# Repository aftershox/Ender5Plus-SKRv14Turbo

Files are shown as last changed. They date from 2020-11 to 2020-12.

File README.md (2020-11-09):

# Ender5Plus-SKRv14Turbo
All things related to my Ender 5 Plus

# 16th October 2020 - _Printer arrives_

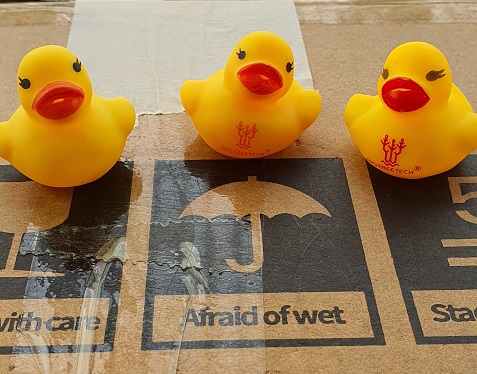
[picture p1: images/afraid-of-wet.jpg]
Image of ducks


**Stock Machine**
BUILT and TESTED - running 1.70.2 firmware from factory.  
- _**BUG found**_ - Auto Home puts NOZZLE and not BL Touch Probe pin at centre of bed.

---

Communicating with the Mainboard
- To connect to the mainboard from PC to USB - have to install FTDI drivers - https://support.th3dstudio.com/hc/en-us/articles/360043291472-Creality-Printer-Drivers-FT232R-Chip-Most-Models
- - Used the FTDI F232R Windows Drivers to create COM port for accessing the Creality Mainboard 
- Use Pronterface to capture existing setup

Firmware for Stock Creality board
- Firmware upgraded to Kersey Fabs Ender-(5PlusBLTouch_0904_V1.71.0 KF.hex) - to fix the BL Touch probe offset (Probe now in centre of bed)
> Watch the video and check Video Description for download links - https://youtu.be/9pDoxf13_wg

- Once Firmware is upgraded - the menus revert back to Chinese Language, so use the control panel / touch screen to set back to English Language. 

# 25th October 2020 - Next job is to install SKR Turbo v.1.4 with 5 x TMC2209s and Z-Steppers auto-align G34 and the BTT TFT 3.5"

1) Set jumpers on SKR v.1.4 Turbo - as per the BTT Guide for TMC 2209 Drivers in UART mode
- - Remove 3 x jumpers from each stepper installation location - leaving just one

2) If NOT using Stallguard / Sensorless Homing - you'll need to CUT the Diag pins on EACH Driver that uses a Physical Limit Switch
- X-UART (Cut Pin / Uses Physical Switch for X Endstop)
- Y-UART (Cut Pin / Uses Physical Switch for Y Endstop)
- Z-UART (CUT PIN / Uses BL Touch Probe as Z- MIN Endstop)
- E0-UART (Cut Pin / Uses Filament Runout Sensor [Physical Switch] with Extruder)
- E1-UART (used for SECOND Z Stepper Motor) - CUT PIN - as BL Touch Probe uses Z- MIN for Z Endstop

- If using 5 x TMC 2209 - i.e. to setup Z2 for using G34 - Z Steppers Auto-Alignment
- - Install TMC 2209 #5 into the E1-UART (Z2) socket
- - E1-UART [Used for Z2-UART) (DO NOT CUT PIN / Uses BL Touch Probe as Endstop)

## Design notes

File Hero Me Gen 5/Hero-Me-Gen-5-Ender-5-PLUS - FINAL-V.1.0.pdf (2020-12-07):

## Installing the HMG5 / Hero Me Gen 5 on the Ender 5 PLUS (Hotend in original build OEM format) 3dpmarkr / aftershox (Github)

This is my guide to installing the Hero Me Gen 5 onto a Creality Ender 5 PLUS – that has not been modified. e.g. Original Hot End housing and fans, as shipped (with no frame modifications). It uses the most compact parts for the smallest footprint, and DUAL 4020 Radial Blowers for maximum CFM / reduced noise overhead as the dual fans can be run as low as 50% without compromising air flow.

TOTAL 3D PRINTED PARTS 7 + 1 OPTIONAL.

GANTRY PARTS
Ender_OEM-MS_Gantry_Adapter_4A

BASE
Hero_Me_Gen5_Base_1

DUCTS
4020_Left_Fan_Mount_Spacer 4020_Lightweight_Duct_Standard_Left

4020_Lightweight_Duct_Standard_Right

ABL – BL TOUCH v.3.1.
BLTouch_Wing_Compact
with the BLTouch_Slider_Compact
X -38, Y+6

OEM 4010 AXIAL FAN COVER (OPTIONAL)
HMG5_Turbine_Fan_Guard

NOTE : The following parts have been chosen to take up the MINIMUM AMOUNT of space. Some of the HMG5 DUCT options protrude too far forward, so with an Ender 5 PLUS – these are the most COMPACT parts. IF you have moved your front TOP extrusion down (for Nozzle visibility) then you may be able to use a different DUCT. If, however, your printer is in the original OEM frame format – then please use the parts list (shown above) to prevent your Hotend crashing into the frame etc.

HMG5 Installation Guide Version 1.0– Written by 3dmarkr / aftershox – 7th December 2020 Page 1 of 28

B.O.M - FANS
2 | x | 4020 Radial Blower – 24V – Dual Ball Bearing type

B.O.M. - Electronics / Connectors / Wire etc.
1 | x | T shape QUICK-Splice Connector.
1 | x | 100mm length Silcone Wire (YELLOW)
- 24 AWG Electrical Wire Kit,0.20mm² Flexible Silicone Wire - rated 300V Hookup
| | Wire High Temperature Resistance
1 | x | 100mm length Silicone Wire (BLUE)
- 24 AWG Electrical Wire Kit,0.20mm² Flexible Silicone Wire - rated 300V Hookup
| | Wire High Temperature Resistance
2 | x | JST.SM 2.54 connectors (2 pin) MALE / FEMALE
1 | x | Tube of Superglue (for securing your nuts!)
2 | x | Small 10mm lengths of heat shrink tubing YELLOW (OPTIONAL)

B.O.M - Screws, bolts & fixings

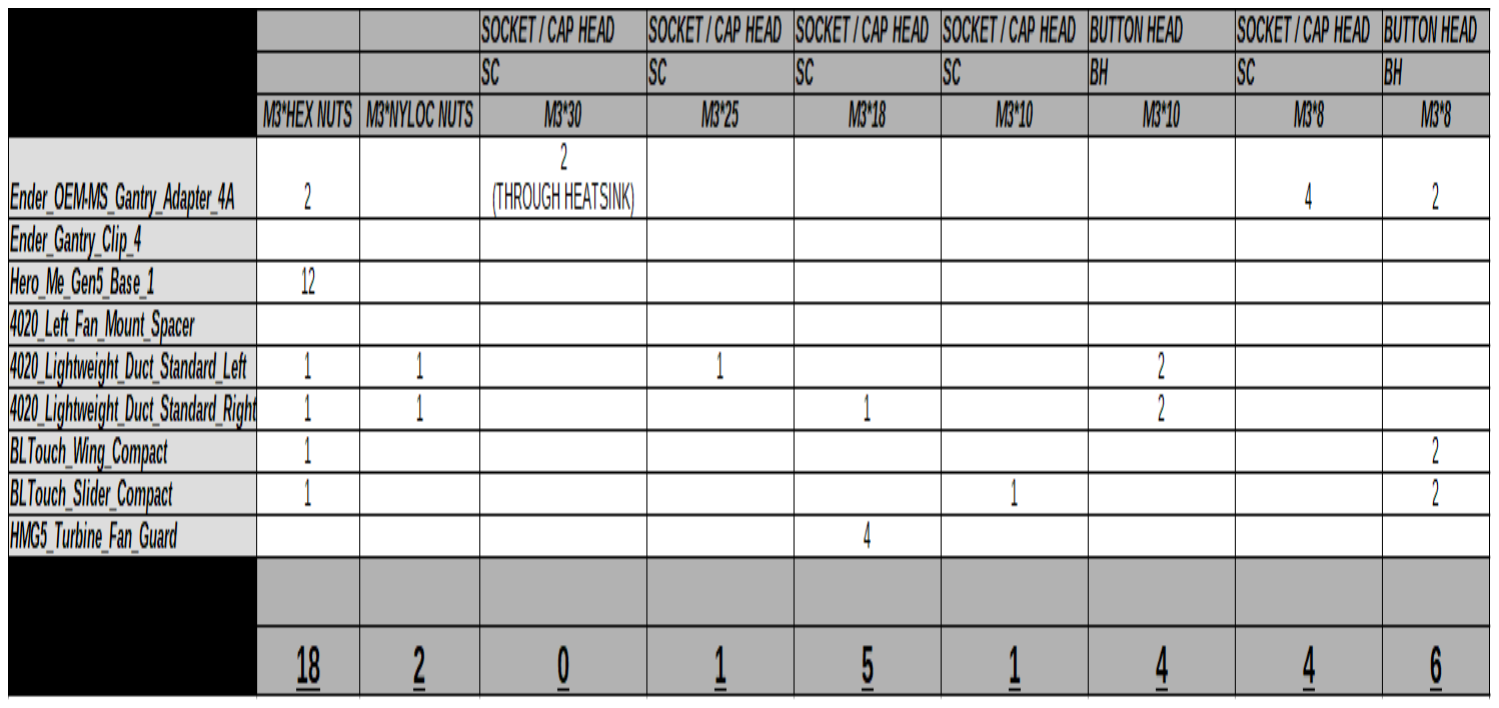
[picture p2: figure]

HMG5 Installation Guide Version 1.0– Written by 3dmarkr / aftershox – 7th December 2020 Page 2 of 28

TOOLS / SUNDRIES

IWISS SN-01BM Ratchet Wire Cable Crimping Pliers Tool 0.08-0.5mm² or SIMILAR Wire Cutters
Hex Keys / Hex Drivers (supplied with printer)
Spanners (in particular, the Nozzle spanner)
3mm drill bit / Cable Ties

### Installation – Notes

Wiring – Preparation

To upgrade from a single 4010 Radial Fan Blower (OEM Parts Fan) to DUAL 2 x 4020 Radial Fan Blower, you’ll need to split the wiring to allow you to run two fans from one original set of wires.

Normally, the 4010 parts fan uses a wiring colour scheme of :-

YELLOW
&
BLUE

New Parts Fans will usually have RED & BLACK wiring, and for consistency purposes – you should always match the following wiring colours.

OEM Fan | | New 4020 Radial Blower
YELLOW | → | RED
BLUE | → | BLACK

STAGE 1 – Disassemble your OEM Hotend

With the printer unplugged, remove all of the screws for the BL Touch Mount, Fan Cover, Fans, and the screws that go through the HEATSINK.

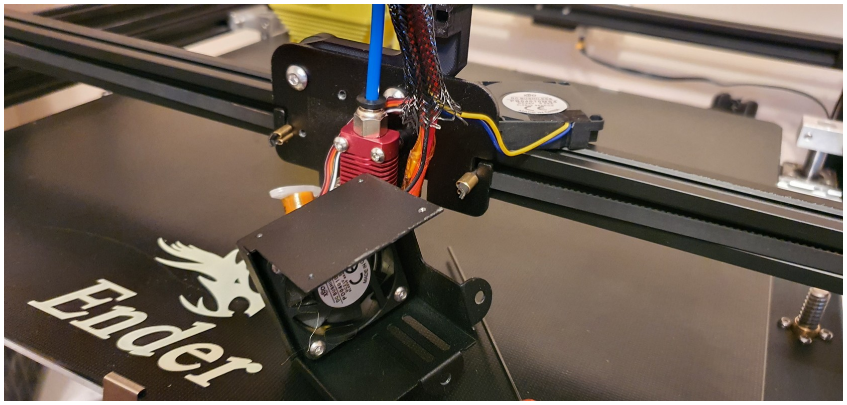
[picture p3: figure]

HMG5 Installation Guide Version 1.0– Written by 3dmarkr / aftershox – 7th December 2020 Page 3 of 28

Using your SNIPS – cut off the 4010 Parts Cooling RADIAL Fan – leave as much wire as possible for the remaining wiring loom. e.g. Leave only around 10mm of wire on the 4010 fan you cut off.

Locate your T shape QUICK-Splice Connector, open BOTH ends in readiness.

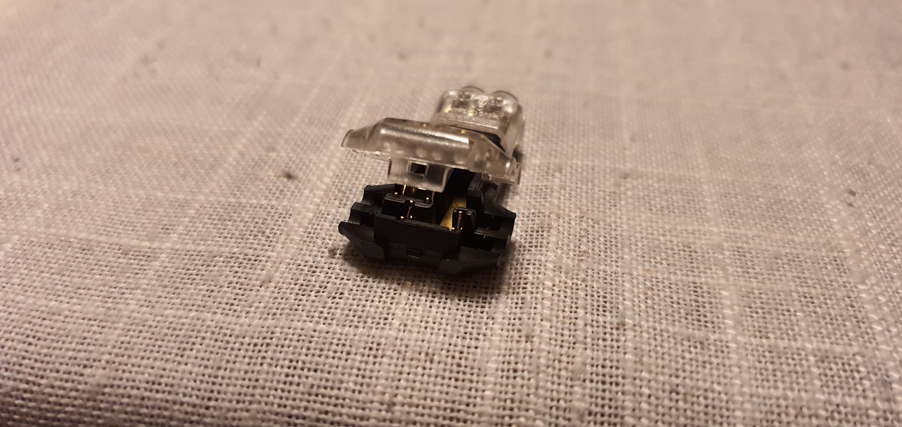
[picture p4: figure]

PREPARE YOUR PRINTER WIRING LOOM

The circuit diagram (below) shows how the BLUE and YELLOW wires should be laid into the connector. IGNORE the RED / BLACK – this just shows you how the circuit path is wired.

NOTE : Lay your 100mm lengths of BLUE / YELLOW Wire across the T shape QUICK-Splice (ENSURE THE WIRES ARE CENTRED – 50mm each side of the connetor), BLUE on top and YELLOW directly underneath. You do not need to prepare the wire, just lay it in the tracks and CLAMP the connector FIRMLY shut..

HMG5 Installation Guide Version 1.0– Written by 3dmarkr / aftershox – 7th December 2020 Page 4 of 28

For the other connector end which will join into your existing wiring, you will need to open the connector end, insert the wires through the small round holes and CLAMP the connector shut FIRMLY. MAKE SURE YOU MATCH THE COLOURS CORRECTLY.

If you have done this correctly, you should now have a T shaped wiring loom connected to your existing printer wiring.

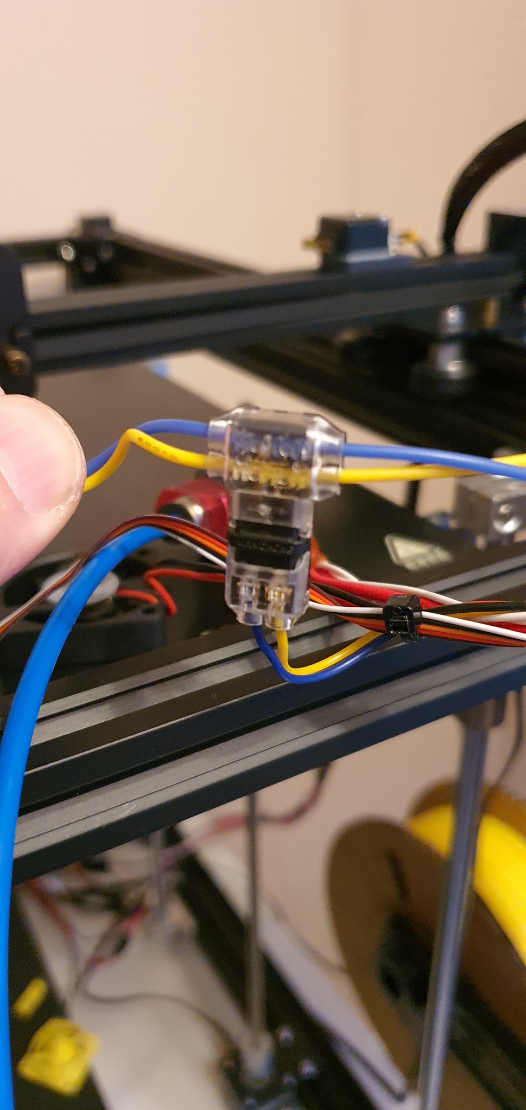
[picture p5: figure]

HMG5 Installation Guide Version 1.0– Written by 3dmarkr / aftershox – 7th December 2020 Page 5 of 28

Figure 1: NOTE : the wire colour on the LEFT at the BOTTOM of the connector should MATCH the TOP wire colour AS PER THE CIRCUIT DIAGRAM.

Using your wire cutters, or strippers – remove around 2-3mm of the cable sheaths (BLUE and YELLOW) from one end of the T splice (LOOM 1).

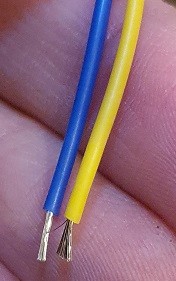
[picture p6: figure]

Locate BOTH of your JST.SM 2.54 pitch connectors, plus 4 x FEMALE (socket) wire ends.

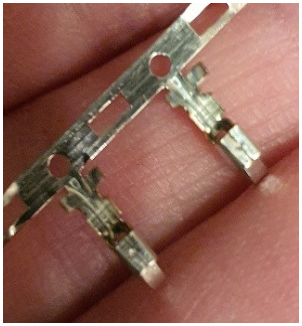
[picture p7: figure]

HMG5 Installation Guide Version 1.0– Written by 3dmarkr / aftershox – 7th December 2020 Page 6 of 28

SNAP OFF and LOAD one of the FEMALE (socket) connectors into your CRIMPING TOOL (IWISS). Two ratchets is usually sufficient holding force.

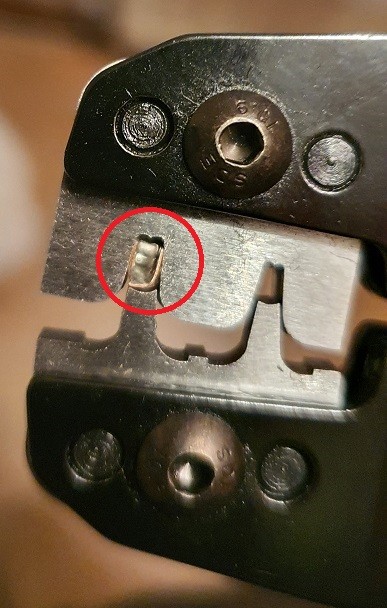
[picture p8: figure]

HMG5 Installation Guide Version 1.0– Written by 3dmarkr / aftershox – 7th December 2020 Page 7 of 28

Here is another view from the FRONT.

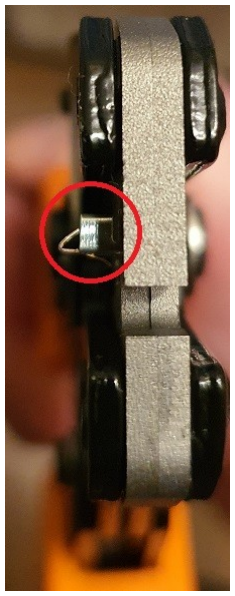
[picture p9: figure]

Insert the YELLOW wire into the FEMALE (socket) wire end INCLUDING around 1mm of the cable with SHEATH (not stripped) – this allows the connector to GRAB on to the wire, and RATCHET CLAMP it down. If you’ve done it correctly, the wire should be nicely secured within the connector. (REPEAT THE PROCESS FOR THE BLUE WIRE).

NOTE : Examine the connectors for any loose strands of wire, if necessary – fold the loose strands back, and snip off with the cutters.

Next – locate the FEMALE PLUG end of the JST.SM (as per the picture below)

HMG5 Installation Guide Version 1.0– Written by 3dmarkr / aftershox – 7th December 2020 Page 8 of 28

Each of the FEMALE (socket) wire connectors has a small locking tab (TANG) which sticks up, the wires should be inserted into the FEMALE PLUG with the TANG up. See image below.

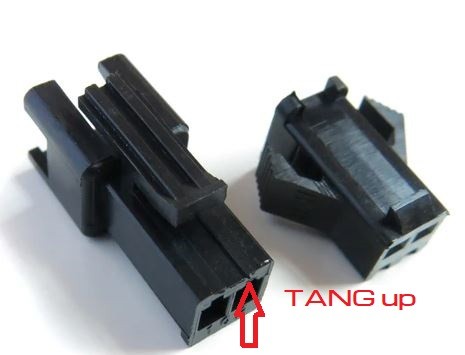
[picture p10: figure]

If you get it wrong, the connector will likely fall out. If you get it correct, it should hold the wire into the connector with a SATISFYING CLICK.

Remember that the LOOM END should ALWAYS use the FEMALE PLUG !

( REPEAT THIS PROCESS FOR THE OTHER FAN LOOM SIDE – for LOOM 2 )

PREPARE THE FANS WIRING

Remove one of your new fans (4020 Radial Blower) from the box, it will have RED / BLACK wiring and a small white connector on the end (this is NOT needed).

Take your snippers and CUT OFF the white connector (leaving as MUCH WIRE as POSSIBLE) on the fan/s. Split the wires Red / Black away from each other – for around 50mm.

(OPTIONAL) – add a small 10mm length of YELLOW heat shrink tubing to the RED cable sheath (helps you to identify which wire is Yellow later on!). Heat the tubing about half way down the wire until it no longer slides up and down the wire.

Locate BOTH of your remaining MALE parts from the JST.SM 2.54 pitch connectors, plus 4 x MALE (PINS) wire ends.

HMG5 Installation Guide Version 1.0– Written by 3dmarkr / aftershox – 7th December 2020 Page 9 of 28

Figure 2: Picture shows MALE connector - TANG UP orientation. For the T loom end (NOT THE FAN Connector wires)

Using your wire cutters, or strippers – remove around 2-3mm of the cable sheaths (RED and BLACK) from one end of FAN 1.

As before, LOAD the JST MALE Crimp Pin into your IWISS Ratchet crimping tool (2 clicks of the ratchet is usually sufficient holding force)

Insert the RED fan wire into the MALE (crimp pin) INCLUDING around 1mm of the cable with SHEATH (not stripped) – this allows the connector to GRAB on to the wire, and RATCHET CLAMP it down. If you’ve done it correctly, the wire should be nicely secured within the connector. (REPEAT THE PROCESS FOR THE BLACK WIRE).

NOTE : Examine the connectors for any loose strands of wire, if necessary – fold the loose strands back, and snip off with the cutters.

You should now have a FAN with two MALE pins crimped on.

HMG5 Installation Guide Version 1.0– Written by 3dmarkr / aftershox – 7th December 2020 Page 10 of 28

Figure 3: JST MALE
Crimp pins

NEXT STEP (VERY IMPORTANT)

Take the MALE end of the JST SM plastic housing and CLIP IT into the FEMALE plastic housing so it locks into place.

Now take your first MALE JST Crimp Pin wire – ENSURING THE TAB / TANG is the correct way up, and MOST IMPORTANTLY – ensure the WIRE COLOURS *MATCH* with the other end. e.g. Your FAN RED WIRE wire should match up with the YELLOW wire on the LOOM END.

Now insert the BLACK wire so it matches up with the BLUE wire on the LOOM END.

( REPEAT THE STEPS ABOVE FOR FAN 2 ). Strip, crimp, insert housings together, and match up wires.

If all is done correctly, the FANS will now be connected using their JST SM connectors into the WIRING LOOM.

TEST THE FANS

With ALL cables and fans dangling (ENSURE NOTHING IS TOUCHING) – power up your printer.

In Marlin Mode, go into the Temperature menu and set the Parts FAN to come on – around 50% or higher (remember to CLICK on the new value, and exit the menu for the fans to come on).

BOTH new fans should BLOW as expected, set the speed back to 0% and the fans should STOP. If all is working OK – then proceed to install the HMG5.

If you have a touch screen display TFT35 or original OEM display – find the appropriate menu for the PARTS fan, and test as per the onscreen menus.

POWER OFF / UNPLUG YOUR PRINTER before proceeding. If you have a problem, then go back and check your wiring / connections before moving to the next stage.

!!! DISCONNECT YOUR * NEW * FANS !!!

HMG5 Installation Guide Version 1.0– Written by 3dmarkr / aftershox – 7th December 2020 Page 11 of 28

INSTALLING THE HMG5

Find the Gantry Plate - Ender_OEM-MS_Gantry_Adapter_4A

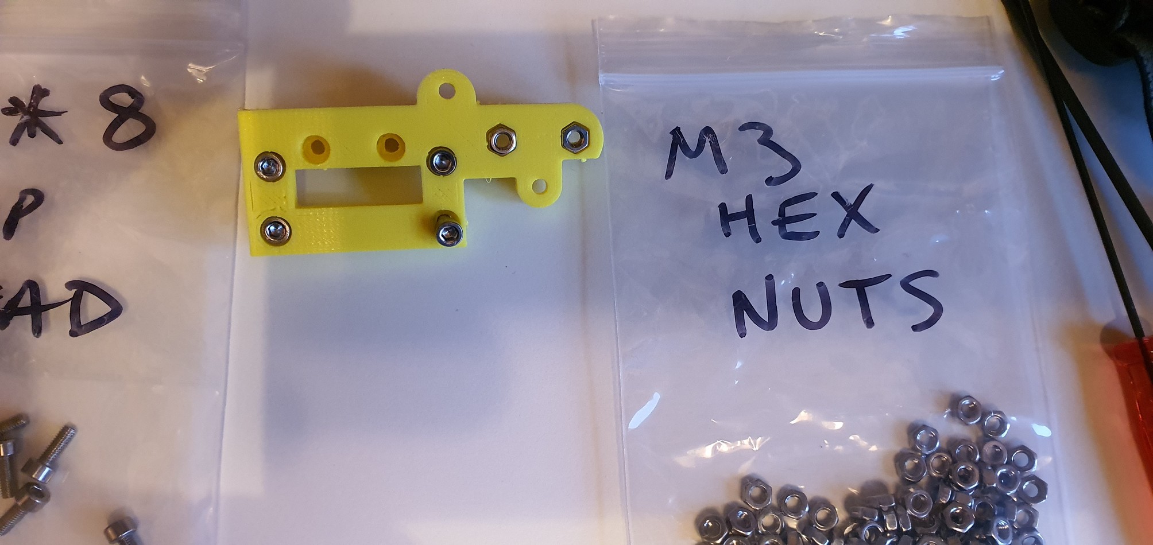
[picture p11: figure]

From the REAR of the plate, insert the 4 x M3*8mm SC through the plate; back to front.

Insert the 2 x M3*Hex Nuts into the rear of the plate – as shown on the right. If the nuts are loose, use a small DAB of superglue.

Find your BASE - Hero_Me_Gen5_Base_1

In the Base – find all of the 12 x locations for the M3*Hex Nuts (and use a dab of glue to secure them into Gen5_Base_1)
- There are 6 on the inside the base (3 each side for the sliding duct channel)
- 4 on the bottom of the base (quite difficult to find – these are the ones that connect the Base to the Gantry Plate)
- 2 at the rear

Using your 2 x M3*30mm SC – loosely secure your original Creality Hotend HEATSINK – to the Ender_OEM-MS_Gantry_Adapter_4A. Loose is OK at the moment, as they will tightened later to the standoffs on the metal plate on the
X Gantry.

Now secure the Ender_OEM-MS_Gantry_Adapter_4A to the Hero_Me_Gen5_Base_1 by tightening the four 4 x M3*8mm SC

HMG5 Installation Guide Version 1.0– Written by 3dmarkr / aftershox – 7th December 2020 Page 12 of 28

Figure 4: 4 x screws at bottom of base from the back / through the plate. THIS CAN BE A LITTLE FIDDLY, but once you get it started – you’ll end up the the Base / Gantry adapter connected together.

You can also attach the BLTouch_Wing_Compact using 2 x M3*8mm BH – as per the photo below.

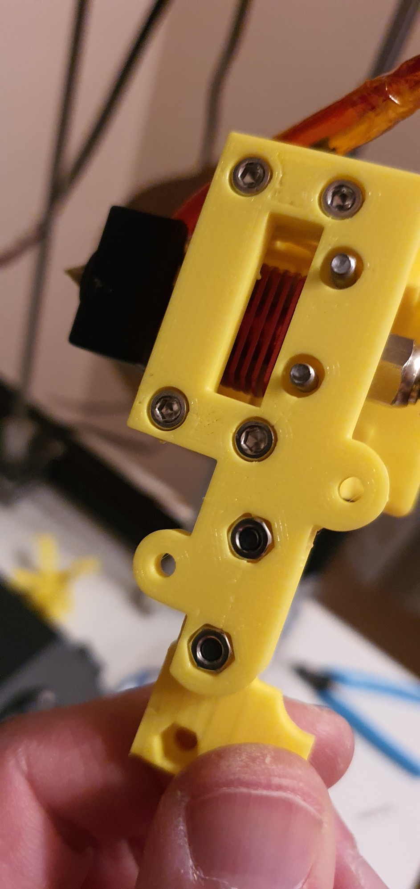
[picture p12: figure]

HMG5 Installation Guide Version 1.0– Written by 3dmarkr / aftershox – 7th December 2020 Page 13 of 28

Offer up the newly joined parts to the metal X Gantry Plate – ensure it is flush with the original gantry plate.

Secure / tighten down the HEATSINK to the standoffs through the holes at the front of the base.

Add 2 x additional M3*8 BH as per the image below. These align with the original holes in the metal backplate.

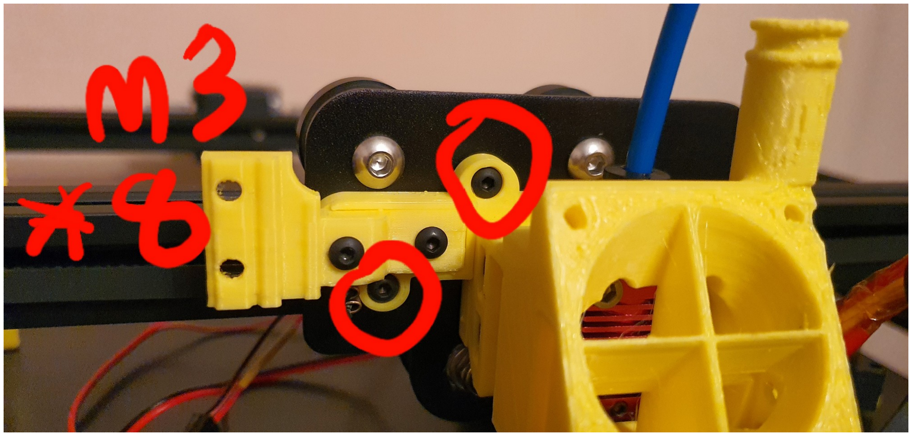
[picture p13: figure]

HMG5 Installation Guide Version 1.0– Written by 3dmarkr / aftershox – 7th December 2020 Page 14 of 28

Next, we’ll put attach the BL Touch to it’s compact bracket. Uses 2 x M3*8mm BH

NOTE the orientation of the BL Touch and wiring loom (it should face backwards when mounted) BEHIND the LEFT DUCT part. It is a tight fit when the LEFT DUCT is installed, but can slide up/ down when setting the height. There is a little cable guide built into the BLTouch_Slider_Compact.

To secure it – you will need

1 | x | M3*HEX Nut (behind the BLTouch_Wing_Compact) *hold it in place whilst tightening
1 | x | M3*10mm SC to secure the BL Touch mount (BLTouch_Slider_Compact) to the wing.

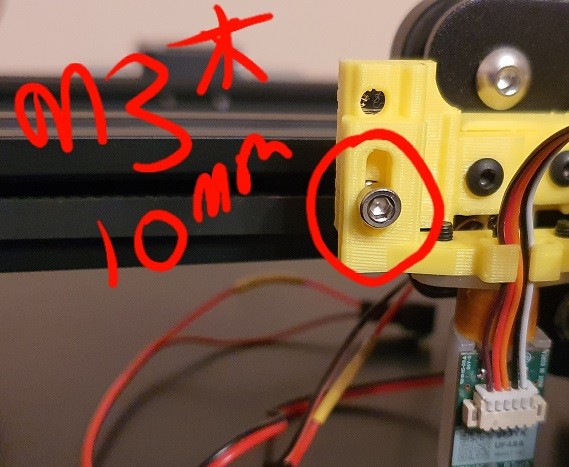
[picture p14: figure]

HMG5 Installation Guide Version 1.0– Written by 3dmarkr / aftershox – 7th December 2020 Page 15 of 28

NEXT – we need the DUCT parts (LEFT and RIGHT)

4020_Lightweight_Duct_Standard_Left

4020_Lightweight_Duct_Standard_Right

Starting with the 4020_Lightweight_Duct_Standard_Left DUCT – align the duct with the main BASE body, and slide it up until the bottom of the duct is approx 15mm above the nozzle.

You will require 2 x M3*10mm BH and 1 x M3*Hex Nut for the LEFT DUCT FRONT fastening,

Loosely tighten the REAR screw of the duct into one of the three M3*nuts that are behind inside the Base.

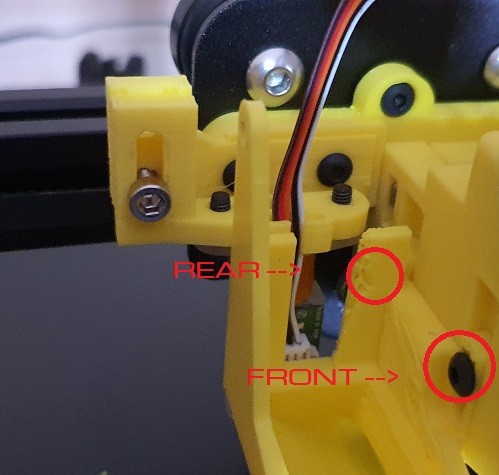
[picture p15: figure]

For the FRONT M3*10mm, and M3*Hex Nut – you need to access the lower LEFT QUARTER hole of the HMG Base part. THIS IS QUITE TRICKY TO FASTEN; The Nut is on the inside, and the M3*10mm screws through the side. Again, fasten loosely at this stage.

( REPEAT THE STEPS ABOVE FOR THE RIGHT SIDE DUCT )

Again, you will need 2 x M3*10mm BH and 1 x M3*Hex Nut for the RIGHT DUCT FRONT fastening.

Repeat the process, align the RIGHT duct with the main BASE body, and slide it up until the bottom of the duct is approx 15mm above the nozzle.

Fasten the REAR fixing.

HMG5 Installation Guide Version 1.0– Written by 3dmarkr / aftershox – 7th December 2020 Page 16 of 28

Using the lower RIGHT QUARTER hole of the HMG Base part. THIS IS QUITE TRICKY TO FASTEN; The Nut is on the inside, and the M3*10mm screws through the side. Again, fasten loosely at this stage.

Locate the NOZZLE spanner that came with your printer. This is approx 1.5mm thickness, and ideal for setting the DUCT heights. The manual suggests between 1.4mm – 1.8mm

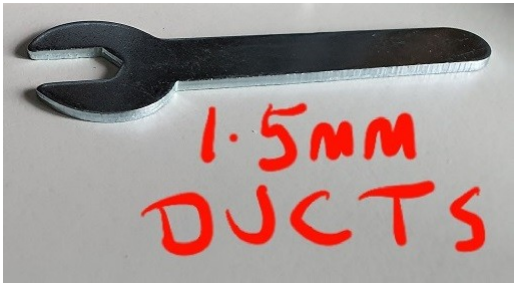
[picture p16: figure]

Move your HOTEND assembly to the centre of the bed.

WITH THE PRINTER OFF - manually RAISE Both Z Axis, by rotating the lead screws until the nozzle is lightly touching the bed.

Put your Nozzle Spanner underneath the LEFT DUCT – this sets the height at 15mm above nozzle.

TIGHTEN the REAR and FRONT retaining screws for the LEFT DUCT.

Move the spanner to the RIGHT HAND DUCT.

HMG5 Installation Guide Version 1.0– Written by 3dmarkr / aftershox – 7th December 2020 Page 17 of 28

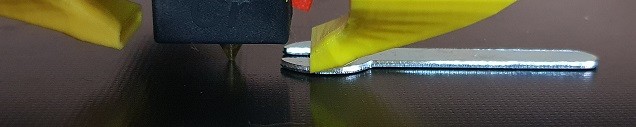
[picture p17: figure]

TIGHTEN the REAR and FRONT retaining screws for the RIGHT DUCT.

Set the BL Touch Height

Now we have finished setting the DUCT heights, we can also set the BL Touch height as well. The BL Touch v.3.1. should be approx 4mm from the bottom of the stored probe to where the nozzle meets the bed.

Luckily, we have just the tool for the job. It is the 4mm HEX Key that came with your printer.

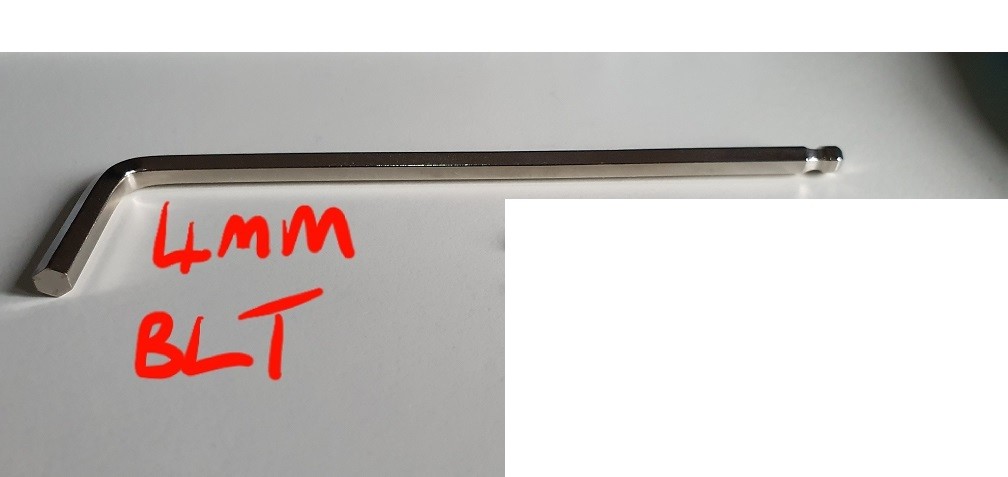
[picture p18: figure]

Slide the 4mm Hex Key underneath the BL Touch probe, and slide it up/down until the BL Touch nozzle is just touching the top of the Hex Key (as per the photo below)

HMG5 Installation Guide Version 1.0– Written by 3dmarkr / aftershox – 7th December 2020 Page 18 of 28

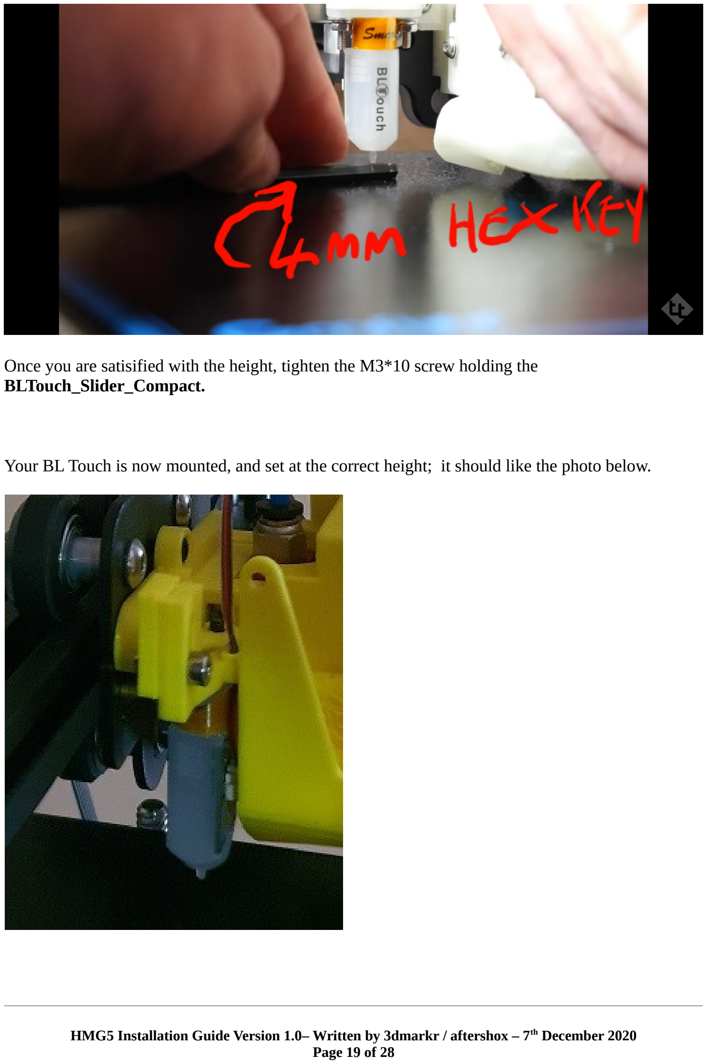
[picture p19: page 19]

Once you are satisified with the height, tighten the M3*10 screw holding the BLTouch_Slider_Compact.

Your BL Touch is now mounted, and set at the correct height; it should like the photo below.

HMG5 Installation Guide Version 1.0– Written by 3dmarkr / aftershox – 7th December 2020 Page 19 of 28

Install front axial fan 4010 and OPTIONAL fan cover

The next step is to install is the front fan, and OPTIONAL fan guard.

IMPORTANT : Ensure all Hotend wires are out of the way before you start !

For this, you will need 4 x M3*18 SC screws; the screws will cut their own thread as you screw them in to the base. CAUTION :- be aware, that the front / upper right fan screw can slightly protrude through into the cable restraint channel. See image below.

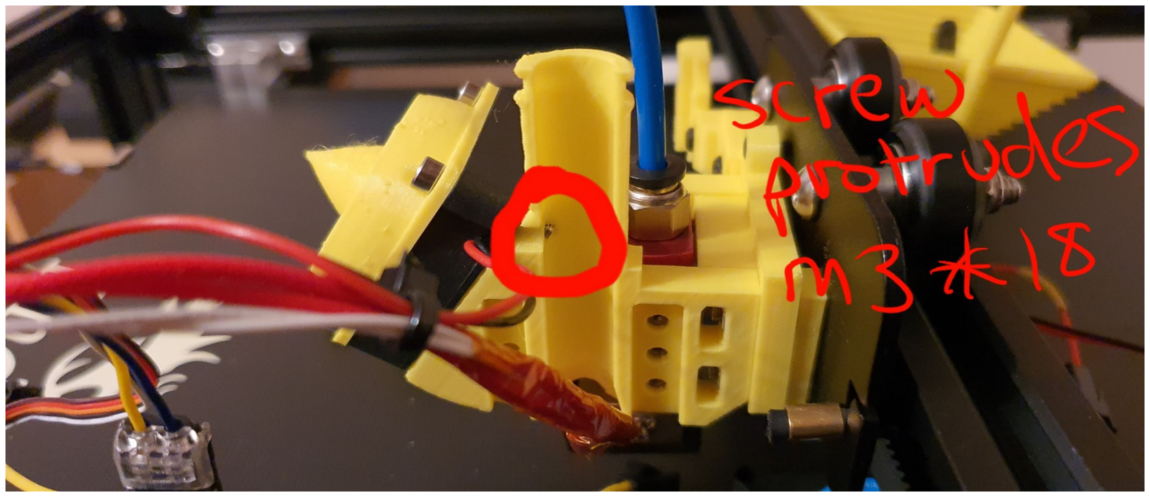
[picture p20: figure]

HMG5 Installation Guide Version 1.0– Written by 3dmarkr / aftershox – 7th December 2020 Page 20 of 28

Figure 5: I removed the RIGHT SIDE DUCT here, to show the protruding screw problem.

Take care NOT to damage any cables. If in doubt, you can always swap the front, upper right screw for a shorter one. e.g. M3*16

Install the LEFT SIDE 4020 Radial Blower Fan

To make installing this fan easier, you may wish to use a 3mm drill bit / hand drill to slightly enlargen the hole in the LEFT DUCT (used for the retaining fan bolt, spacer & nyloc nut).

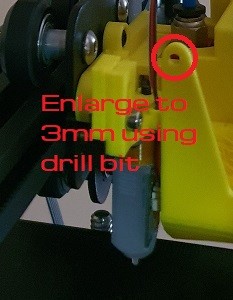
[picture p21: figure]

Drill / enlarge this hole out to 3mm.

Place the new fan into the LEFT DUCT, and route the wires accordingly.

For installing this fan, you will need :-

1 | x | M3*25mm SC
1 | x | 4020 Blower Spacer (3D printed) - 4020_Left_Fan_Mount_Spacer
1 | x | M3*NYLOC Nut

HMG5 Installation Guide Version 1.0– Written by 3dmarkr / aftershox – 7th December 2020 Page 21 of 28

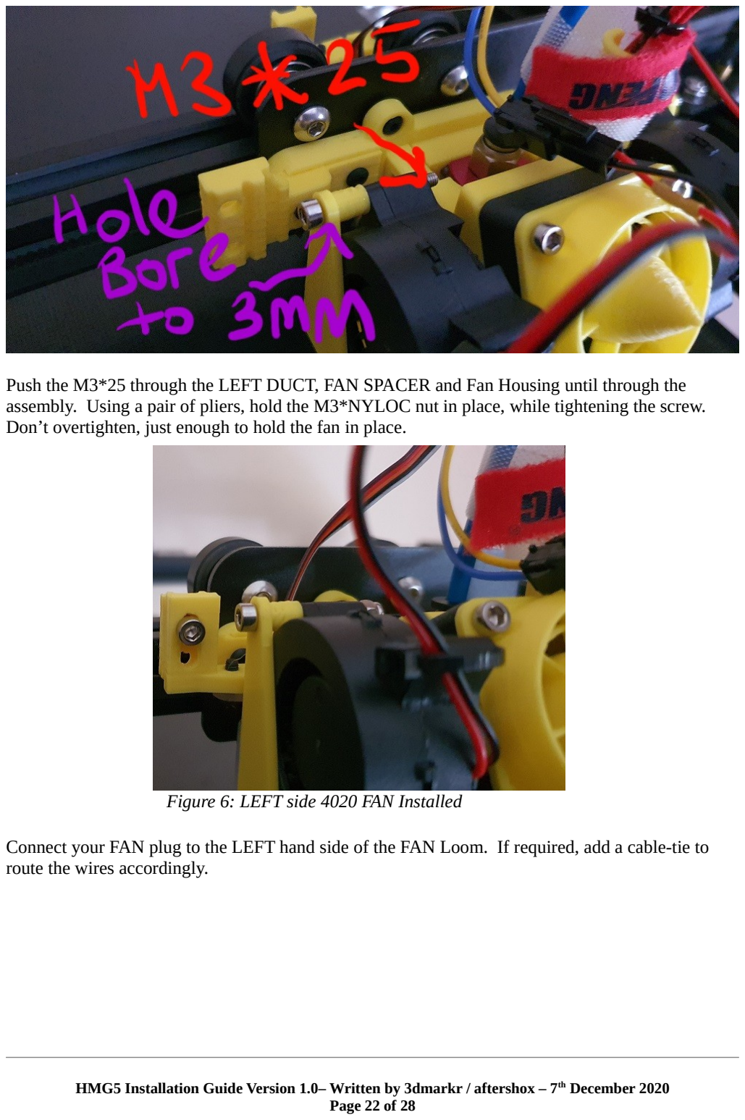
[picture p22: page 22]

Push the M3*25 through the LEFT DUCT, FAN SPACER and Fan Housing until through the assembly. Using a pair of pliers, hold the M3*NYLOC nut in place, while tightening the screw. Don’t overtighten, just enough to hold the fan in place.

Connect your FAN plug to the LEFT hand side of the FAN Loom. If required, add a cable-tie to route the wires accordingly.

HMG5 Installation Guide Version 1.0– Written by 3dmarkr / aftershox – 7th December 2020 Page 22 of 28

Figure 6: LEFT side 4020 FAN Installed

Install the right hand side 4020 Fan Blower

The right hand side fan is easier, again – enlarge the hole in the RIGHT DUCT to 3mm.

Drop the blower into the DUCT,

For this FAN, you will need :-

1 | x | M3*18mm SC
1 | x | M3*NYLOC Nut

Using a pair of pliers, hold the M3*NYLOC nut in place, while tightening the screw. Don’t overtighten, just enough to hold the fan in place.

Connect your FAN plug to the RIGHT hand side of the FAN Loom. If required, add a cable-tie to route the wires accordingly.

HMG5 Installation Guide Version 1.0– Written by 3dmarkr / aftershox – 7th December 2020 Page 23 of 28

Figure 7: RIGHT side FAN installed

TIDY UP THE CABLES

Using cable-ties – tidy up, and route your wiring accordingly.

POWER-UP AND TEST FANS (AGAIN!)

BEFORE we make the final changes to our offsets, it is worthwhile checking the fans are still working correctly.

In Marlin Mode, go into the Temperature menu and set the Parts FAN to come on – around 50% or higher (remember to CLICK on the new value, and exit the menu for the fans to come on).

BOTH new fans should BLOW as expected, set the speed back to 0% and the fans should STOP. If all is working OK – then proceed to install the HMG5.

If you have a touch screen display TFT35 or original OEM display – find the appropriate menu for the PARTS fan, and test as per the onscreen menus.

YOU CAN LEAVE YOUR PRINTER POWERED ON, AS WE WILL NOW NEED TO MAKE CHANGES TO THE OFFSETS FOR THE NEW HOTEND COOLING / BLOWER SYSTEM.

MODIFY THE PROBE OFFSETS FOR THE HMG5

The HMG5 user manual contains the Offsets needed:-

In our example, we have used the following parts:-

BLTouch_Wing_Compact with the BLTouch_Slider_Compact

This gives us a proposed NEW OFFSET values of X -38, Y+6 which need to be SET and STORED in the printer firmware.

HMG5 Installation Guide Version 1.0– Written by 3dmarkr / aftershox – 7th December 2020 Page 24 of 28

Using PRONTERFACE or a similar G CODE Terminal – enter the following TWO commands :-

M851 X-38 Y6

M500

NOTE : M851 sets the PROBE offsets for X, and Y – followed by M500 to STORE the new settings into firmware.

NOZZLE not in correct place after HOMING?

As the gantry adapter pushes the Hotend assembly FORWARD a few mm, it maybe necessary to make some additional changes to the HOMING values.

You can set the Home setting via your slicer software. Based upon the Gantry Adapter you are using, you may need to adjust the Y axis offset.

IF REQUIRED – enter the following TWO commands using your G CODE terminal.

M206 Y-6

M500

Note : This adjusts your Y axis offset M206, and stores it using M500. IMPORTANT : Power OFF / ON – and AUTO HOME to check if the NEW Y Offset has been stored.

In case these values do not place the hotend’s nozzle just inside the edge of the build plate
when homing the Y axis, you can adjust the Y offset value up or down to work for your setup.

The Marlin firmware detailed instructions on setting the printer’s Home offset are here: https://marlinfw.org/docs/gcode/M206.html

HMG5 Installation Guide Version 1.0– Written by 3dmarkr / aftershox – 7th December 2020 Page 25 of 28

BEFORE RUNNING A COMPARISON PRINT

As we’ve made changes to the Hotend system, and have been moving the Z Axis around – some things may have moved from our previous setup.

BEFORE running a comparison print – you’ll likely need to reset / change / set ONE or MORE of the following :-

- Probe Z Offset
- G34 Auto Alignment
- Bed Levelling

We suggest the following order :-

G34 Auto Z Alignment (ONLY if you have dual Z / dual steppers and G34 enabled in firmware)

Pre-heat your machine to an appropriate temperature - i.e. 200 nozzle / 60 bed
From the "Motion" menu, choose "Auto Z Align"
wait until the LCD display reports "Accuracy Achieved" (If this fails - Level your bed, and re-try)

Level your bed (All printers)

Pre-heat your machine to an appropriate temperature - i.e. 200 nozzle / 60 bed

From the "Motion" menu, choose "Level Corners"

Follow the procedure for levelling your bed corners / centre
- Once complete, select "Level Bed" from the menu (Your bed levelling procedure will now measure n/25 points)
- Once complete, choose "STORE SETTINGS" to store the G34 / Mesh Data from the bed levelling procedures.

AUTO-HOME your printer

Z Probe Offset Wizard (All printers with this Marlin feature ENABLED)
Under "Temperature" - lower the temperature of your hot-end to 150 degrees C (it needs to be WARM, but not oozing filament!)

Wait until the Hotend reaches the new lower temperature

Clean your NOZZLE (a dirty nozzle can interfere with Z Probe offset measurements in next step)

Run the "Probe Offset Wizard" from the LCD menu - "Probe Offsets" menu - to correctly set your Z Probe Offset

Follow the on-screen instructions.

HMG5 Installation Guide Version 1.0– Written by 3dmarkr / aftershox – 7th December 2020 Page 26 of 28

Remember to "Store Settings" once complete.

COOLDOWN
From the "Temperature" menu, select "Cooldown"

TEST PRINT
FINALLY - load up, and print a bed tramming / 1st layer test gCode - to ensure your printer is dialled in (especially your Z Offset)

While it is printing - you can DOUBLE-CLICK the knob / selector wheel to access the Probe Z Offset values, and rotate left / right to "fine-tune" the value (includes Babystepping Z)

CONGRATULATIONS - YOUR ENDER 5 PLUS IS NOW READY TO USE.

Don't forget to "tune" your printer.

Advantages to DUAL BLOWERS

One advantage of running twin blowers is the ability to run them on a lower speed / power WITHOUT compromising airflow / CFM.

In your slicer programme - setting your PARTS COOLING (for Dual 4020) to 50% can often run MUCH quieter than running a single 4010 radial blower on full power / speed 100%.

Better cooling, lower noise output. If you need the extra cooling, then of course you can increase the values 50%+ to improve your bridging, and overhangs etc.

## - - finished - -

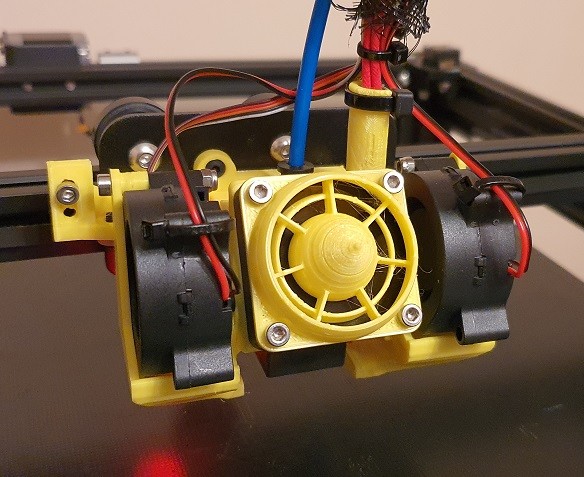
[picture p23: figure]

HMG5 Installation Guide Version 1.0– Written by 3dmarkr / aftershox – 7th December 2020 Page 27 of 28

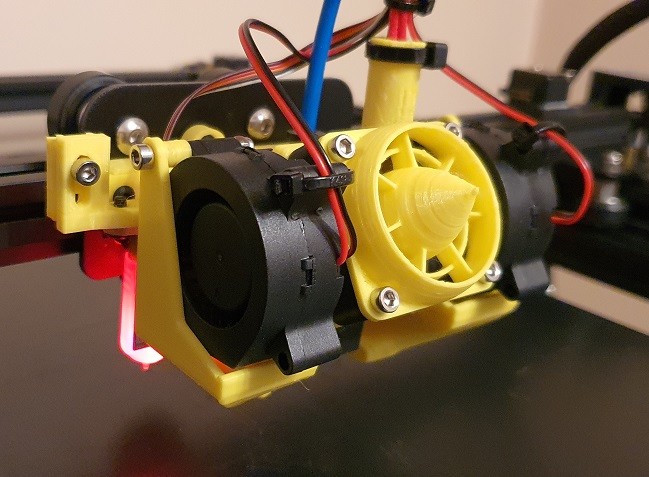
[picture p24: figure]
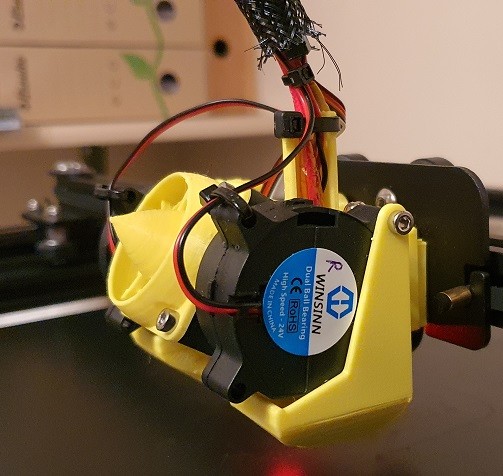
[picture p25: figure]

HMG5 Installation Guide Version 1.0– Written by 3dmarkr / aftershox – 7th December 2020 Page 28 of 28

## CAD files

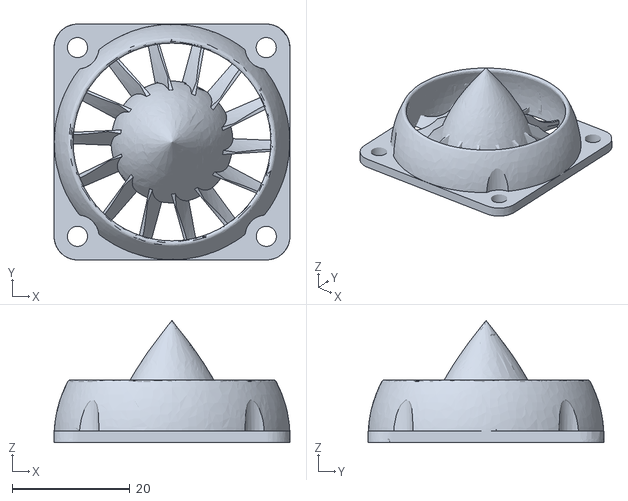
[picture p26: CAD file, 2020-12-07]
Hero Me Gen 5/parts to print/HMG5_Turbine_Fan_Guard.stl
40.0 x 40.0 x 20.7

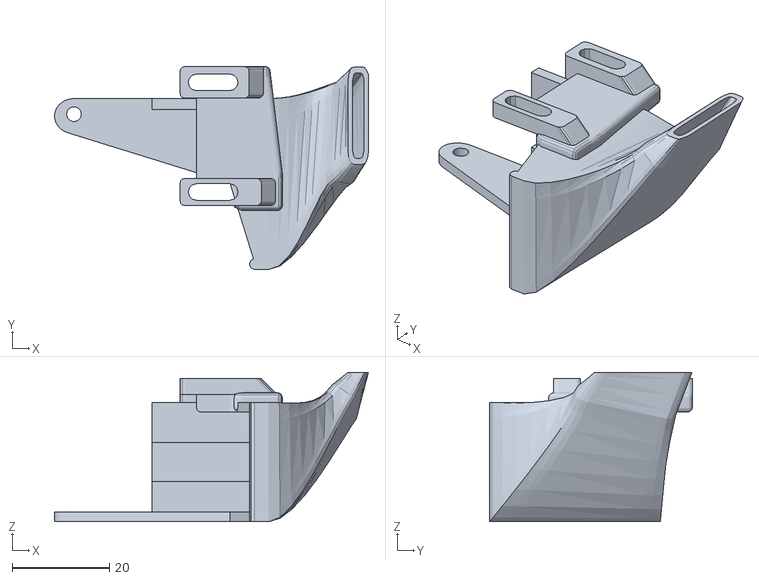
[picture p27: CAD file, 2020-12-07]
Hero Me Gen 5/parts to print/4020_Lightweight_Duct_Standard_Left.stl
64.5 x 41.7 x 30.7

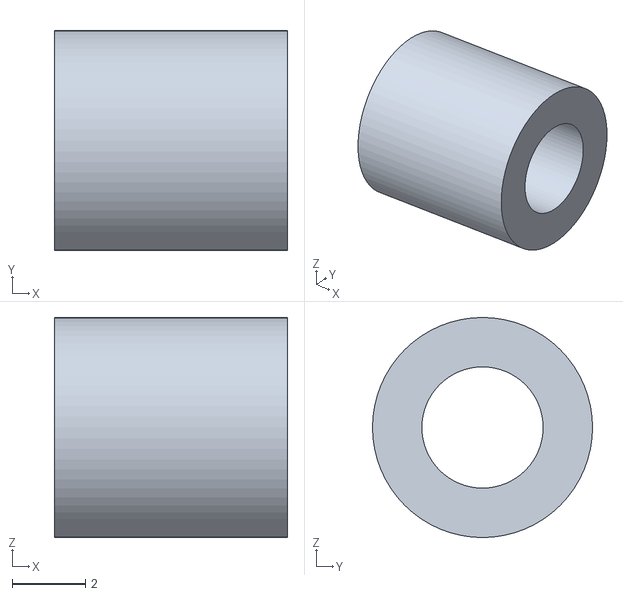
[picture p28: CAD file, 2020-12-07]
Hero Me Gen 5/parts to print/4020_Left_Fan_Mount_Spacer.stl
6.35 x 6.00 x 6.00

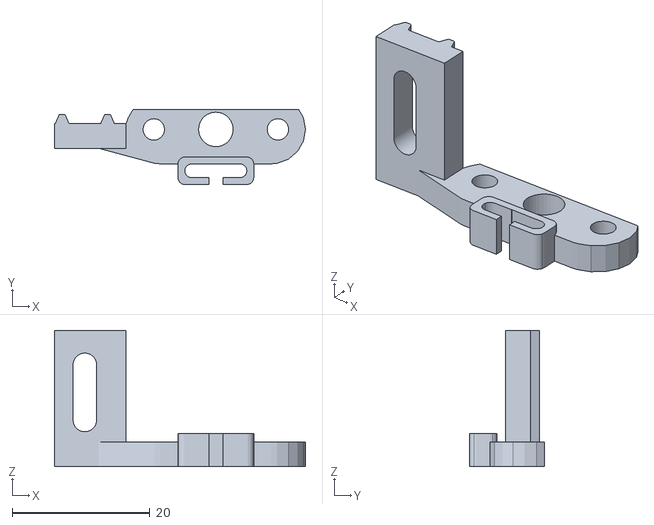
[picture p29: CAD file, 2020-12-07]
Hero Me Gen 5/parts to print/BLTouch_Slider_Compact.stl
36.4 x 10.9 x 19.8

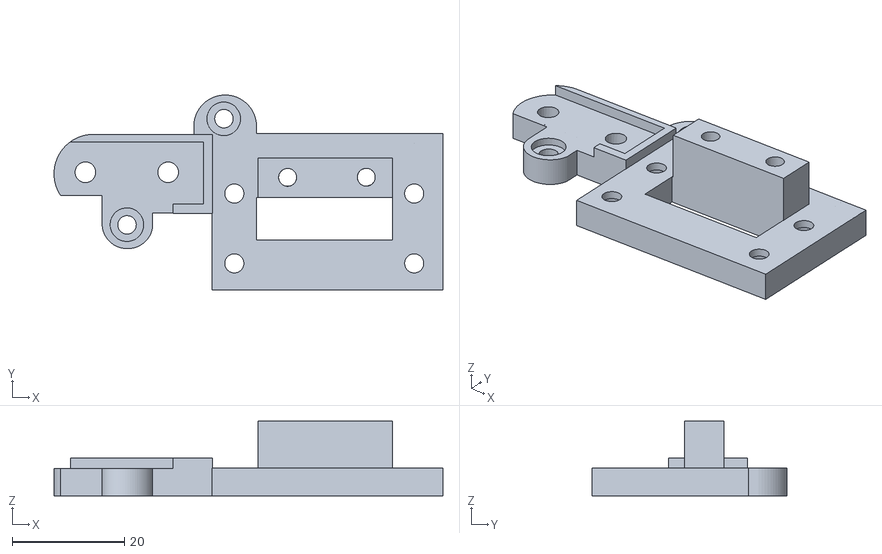
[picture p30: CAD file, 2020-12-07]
Hero Me Gen 5/parts to print/Ender_OEM-MS_Gantry_Adapter_4A.stl
69.3 x 34.7 x 13.3

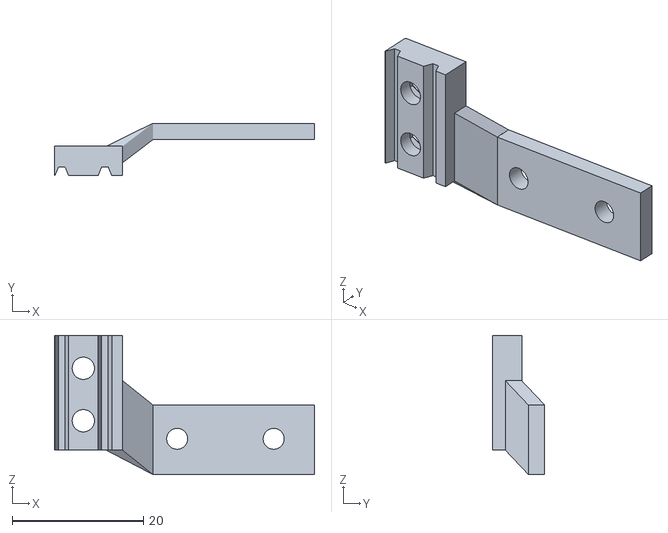
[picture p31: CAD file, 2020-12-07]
Hero Me Gen 5/parts to print/BLTouch_Wing_Compact.stl
39.6 x 8.00 x 21.2

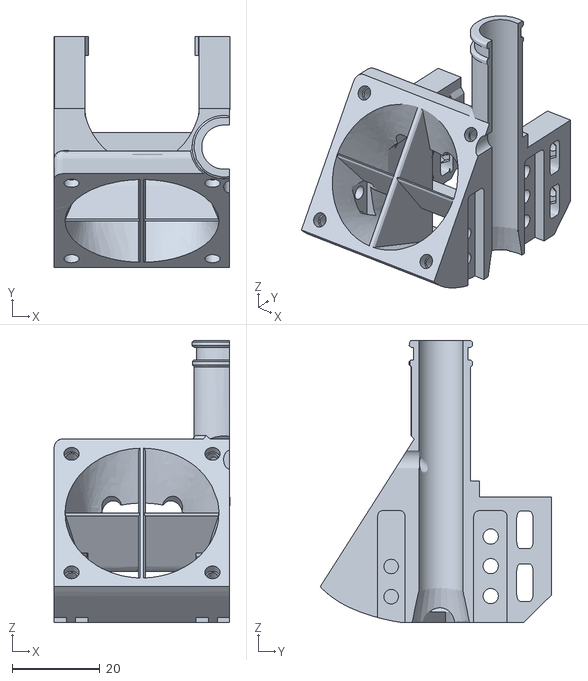
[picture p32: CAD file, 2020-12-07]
Hero Me Gen 5/parts to print/Hero_Me_Gen5_Base_1.stl
40.0 x 52.7 x 64.2

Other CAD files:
Hero Me Gen 5/parts to print/4020_Lightweight_Duct_Standard_Right.stl
